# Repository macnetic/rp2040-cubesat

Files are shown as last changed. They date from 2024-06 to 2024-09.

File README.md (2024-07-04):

# rp2040-cubesat

> [!NOTE]  
> Preview this project on your browser with [KiCanvas](https://kicanvas.org/?github=https%3A%2F%2Fgithub.com%2Fmacnetic%2Frp2040-cubesat)!

## Requirements

| ID  | DESCRIPTION |
|-----|---|
| 001 | Device shall include a minimum of one RP2040 integrated circuit. |
| 002 | Dimensions shall conform with PCI/104 form factor. |
| 003 | Device shall supply 1 external UART interface. |
| 004 | Device shall supply 1 external CAN interface. |
| 005 | Device shall supply 1 on-board SPI interface. |
| 006 | Device shall supply 1 on-board I2C interface. |
| 007 | Device shall use a TCXO to generate a stable reference clock. |

## External interfaces

- UART (PHY TBD)
- CAN
- ARM CoreSight-10

## Schematic strategy

The schematics for this project is laid out across multiple sheets. 
The top-level sheets contain functional block diagrams. 
The functional circuit blocks themselves are implemented in the lower-level sheets.

## PCB Layout strategy

A 4-layer controlled impedance stackup is used.

|Layer | Designation |
|---|---|
| L1 (Top) | SIG |
| L2 | GND |
| L3 | GND |
| L3 (Bottom)| SIG+PWR |

Functional circuit blocks are routed first. The blocks are then laid out and connected.

High-speed electrical interfaces are routed with controlled impedance transmission lines.

Priority is given to routing high-speed interfaces.

Sensitive analog circuitry is separated from digital circuitry.

## References

[1] [CubeSat Information - CubeSat.org](https://www.cubesat.org/cubesatinfo)

[2] [CubeSat Kit PCB Specification](https://web.archive.org/web/20220302180556/http://www.cubesatkit.com/docs/CSK_PCB_Spec-A5.pdf) (archived from the original at http://www.cubesatkit.com/docs/CSK_PCB_Spec-A5.pdf)

[3] [RP2040 Documentation](https://www.raspberrypi.com/documentation/microcontrollers/rp2040.html)

[4]

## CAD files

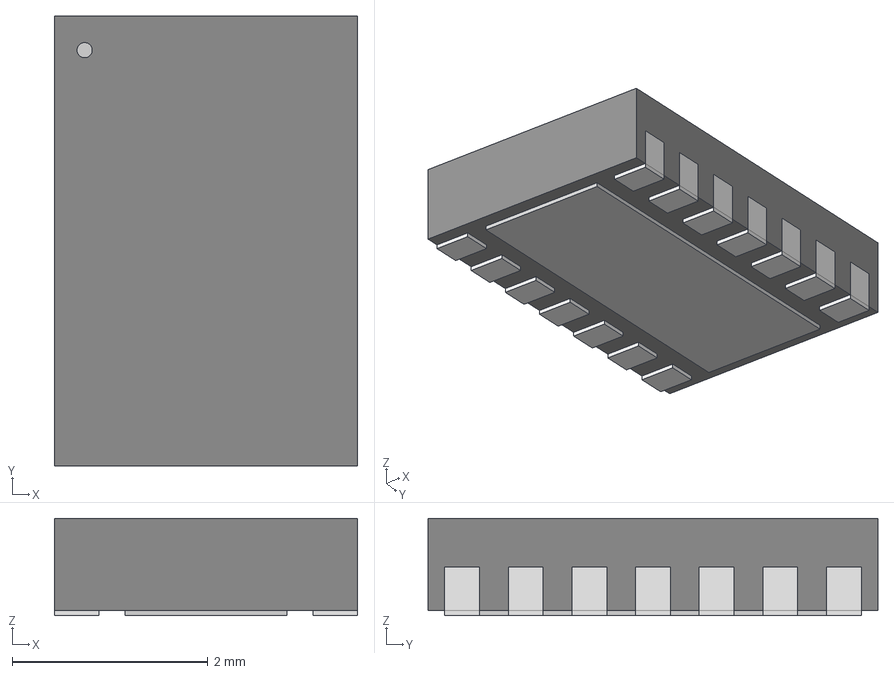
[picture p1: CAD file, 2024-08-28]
footprints/HVSON14_TJA1059_NXP.step
3.10 x 4.60 x 0.993 mm

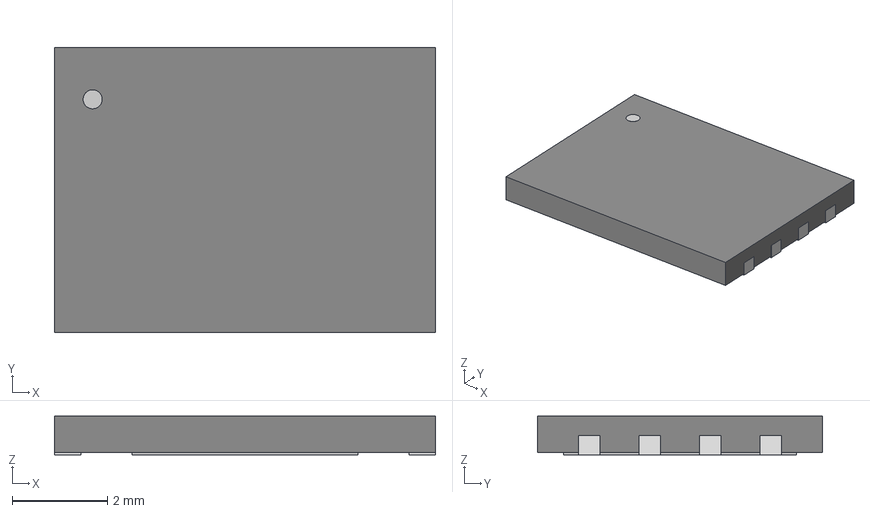
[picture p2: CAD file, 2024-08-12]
footprints/SON8_S25FL128SAGNFI001_INF.step
8.00 x 5.99 x 0.815 mm

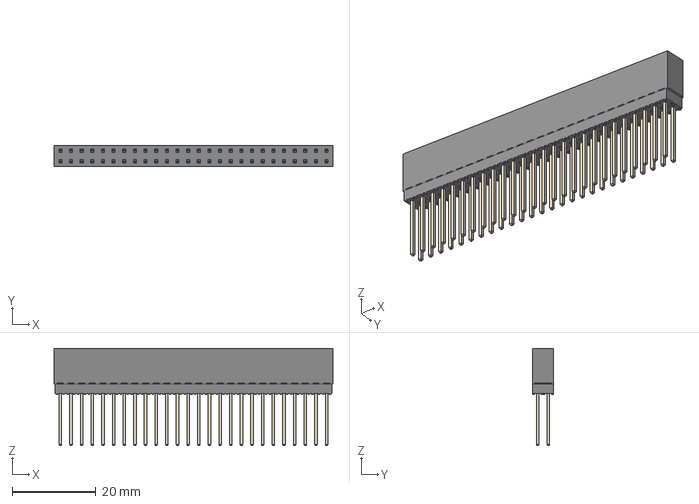
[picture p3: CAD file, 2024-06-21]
footprints/ESQ-126-39-G-D.step
66.5 x 5.08 x 23.2 mm

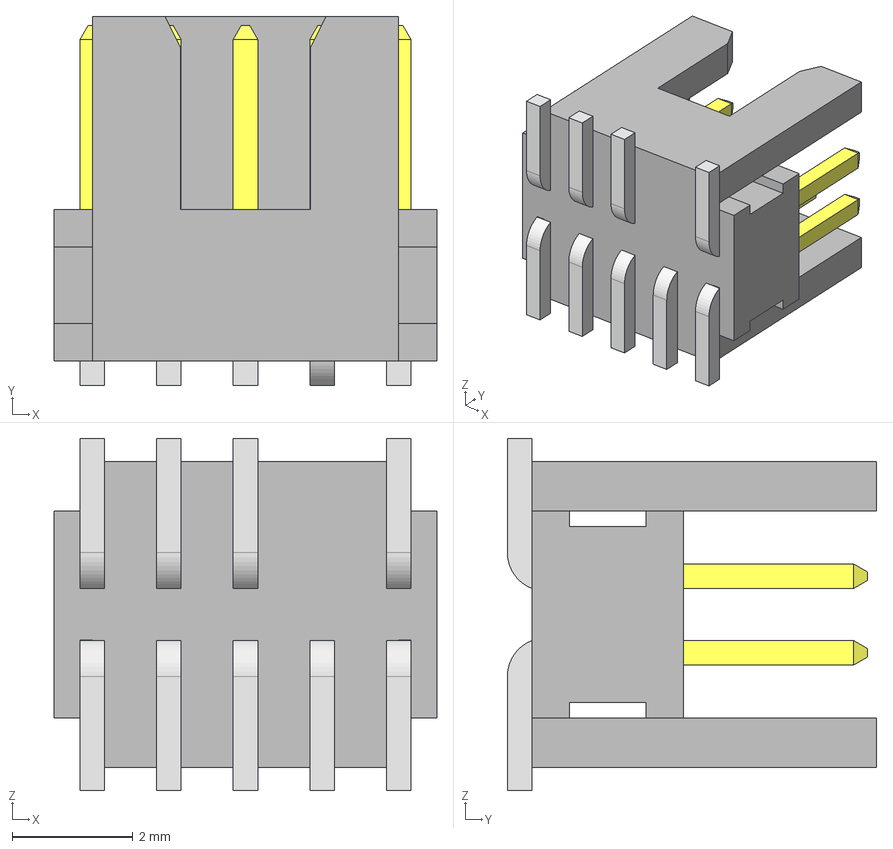
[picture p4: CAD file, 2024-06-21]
footprints/FTSH-105-01-L-DV-007.step
6.35 x 6.12 x 5.84 mm
FTSH-105-01-L-DV-007-K_pins2
FTSH-105-01-L-DV-007-K_pins1
FTSH-105-01-L-DV-007-K_body

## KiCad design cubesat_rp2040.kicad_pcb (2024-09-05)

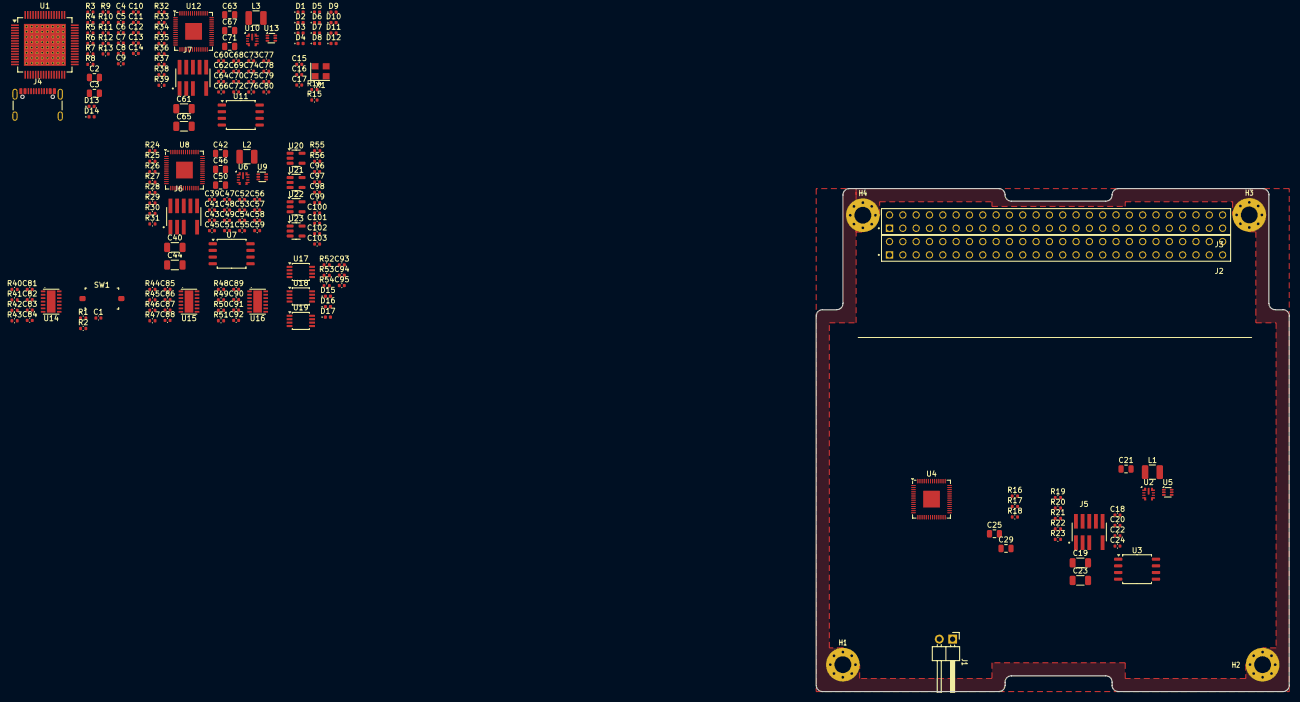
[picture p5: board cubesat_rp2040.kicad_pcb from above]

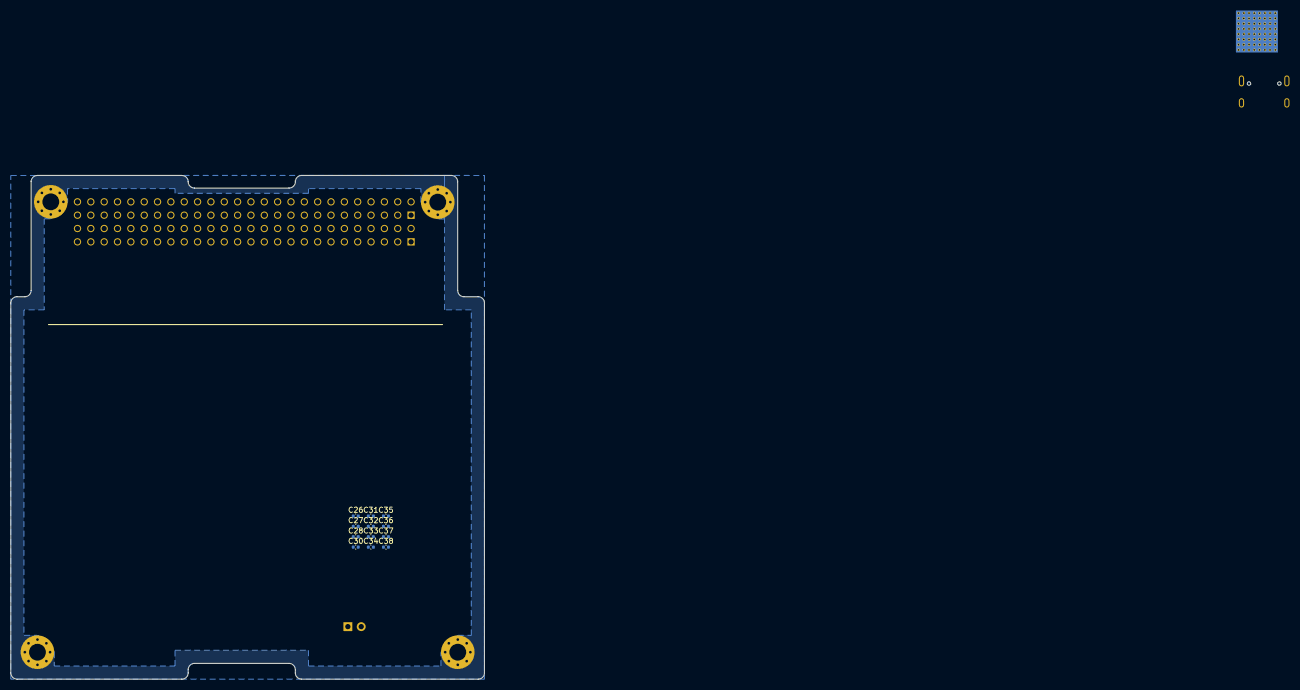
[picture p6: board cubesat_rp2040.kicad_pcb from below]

Board: 6 copper layers, 90.2 x 95.9 mm, 215 parts (12 on the bottom side), 138 nets, no tracks yet.

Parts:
C1, C4, C5, C6, C7, C8, C9, C10, C11, C12, C13, C14, C15, C16, C18, C20, C22, C24, C26, C27, C28, C30, C31, C32, C33, C34, C35, C36, C37, C38, C39, C41, C43, C45, C47, C48, C49, C51, C52, C53, C54, C55, C56, C57, C58, C59, C60, C62, C64, C66, C68, C69, C70, C72, C73, C74, C75, C76, C77, C78, C79, C80, C81, C82, C85, C86, C89, C90, C93, C94, C95, C96, C97, C98, C99: 100nF; C_0402_1005Metric
C2, C3, C21, C25, C29, C42, C46, C50, C63, C67, C71: 1uF; C_0805_2012Metric
C17: 15pF; C_0402_1005Metric
C19, C23, C40, C44, C61, C65: 10uF; C_1206_3216Metric
C83, C84, C87, C88, C91, C92: 4.7nF; C_0402_1005Metric
C100, C101, C102, C103: 1nF; C_0402_1005Metric
D1, D2, D3, D4, D5, D6, D7, D8, D9, D10, D11, D12, D13, D14: D_TVS; D_0402_1005Metric
D15, D16, D17: RED; LED_0402_1005Metric
H1, H2, H3, H4: MountingHole_Pad; MountingHole_3.2mm_M3_Pad_Via
J1: Conn_01x02; PinHeader_1x02_P2.54mm_Horizontal
J2, J3: ESQ-126-39-G-D; SAMTEC_ESQ-126-39-G-D_CUBESAT
J4: USB_C_Receptacle_USB2.0; USB_C_Receptacle_GCT_USB4105-xx-A_16P_TopMnt_Horizontal
J5, J6, J7: FTSH-105-01-L-DV-007-K; SAMTEC_FTSH-105-01-L-DV-007
L1, L2, L3: 15uH; L_1210_3225Metric
R1, R19, R20, R21, R22, R23, R27, R28, R29, R30, R31, R35, R36, R37, R38, R39: 100kR; R_0402_1005Metric
R2: 10kR; R_0402_1005Metric
R3, R4: 5.1kR 10%; R_0402_1005Metric
R5: 90.9kR 1%; R_0402_1005Metric
R6, R9, R10, R11, R12, R13: 4.7kR; R_0402_1005Metric
R7: 10kR 1%; R_0402_1005Metric
R8: 9.53kR 1%; R_0402_1005Metric
R14: 33R; R_0402_1005Metric
R15: 88.7R; R_0402_1005Metric
R16, R24, R32: 1kR; R_0402_1005Metric
R17, R18, R25, R26, R33, R34: 27R; R_0402_1005Metric
R40, R41, R42, R43, R44, R45, R46, R47, R48, R49, R50, R51: 60R; R_0402_1005Metric
R52, R53, R54: 470R; R_0402_1005Metric
R55, R56: 100R; R_0402_1005Metric
SW1: SW_Push; SW_Push_SPST_XKB_TS-1101-X-X
U1: TUSB4041I; HTQFP-64-1EP_10x10mm_P0.5mm_EP8x8mm_Mask4.4x4.4mm_ThermalVi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
U2, U6, U10: LMR36503MSC3RPERQ1; TI_VQFN-HR_2.1x2.1mm_P0.5mm
U3, U7, U11: IS25LP128F; SOIC-8_5.275x5.275mm_P1.27mm
U4, U8, U12: RP2040; QFN-56-1EP_7x7mm_P0.4mm_EP3.2x3.2mm
U5, U9, U13: 74LVC1G11; SOT-563
U14, U15, U16: TCAN1048AV-Q1; SOT1086-2_HVSON14_4.5x3x0.85mm_P0.65mm
U17, U18, U19: 74LVC2G38; TSSOP-8_3x3mm_P0.65mm
U20, U21: SN65LVDS1DBV; SOT-23-5
U22, U23: SN65LVDS2DBV; SOT-23-5
X1: YSO140TC; Oscillator_SMD_YXC_YSO140TC_4Pin_3.2x2.5mm

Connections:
+1V1: C2.1, C4.1, C5.1, C6.1, C7.1, C8.1, C9.1, C10.1, U1.19 (VDD), U1.25 (VDD), U1.37 (VDD), U1.45 (VDD), U1.53 (VDD), U1.60 (VDD), U1.63 (VDD)
+3V3: C3.1, C11.1, C12.1, C13.1, C14.1, C82.1, C86.1, C90.1, C93.1, C94.1, C95.1, R1.1, R14.1, R52.1, R53.1, R54.1, U1.2 (VDD33), U1.20 (VDD33), U1.31 (VDD33), U1.48 (VDD33), U14.11 (VIO), U15.11 (VIO), U16.11 (VIO), U17.8 (VCC), U18.8 (VCC), U19.8 (VCC)
+5V: C81.1, C85.1, C89.1, U14.3 (VCC), U15.3 (VCC), U16.3 (VCC)
/BOOTSEL: J1.1, R16.2, R24.2, R32.2
/CAN PHY - UNIT A/CAN_A.N: D2.2 (A2), J2.01, R41.1, R45.1, R49.1, U14.12 (CANL1), U15.12 (CANL1), U16.12 (CANL1)
/CAN PHY - UNIT A/CAN_A.P: D1.2 (A2), J2.03, R40.1, R44.1, R48.1, U14.13 (CANH1), U15.13 (CANH1), U16.13 (CANH1)
/CAN PHY - UNIT A/CAN_A.RXD: U4.16 (GPIO13), U14.4 (RXD1)
/CAN PHY - UNIT A/CAN_A.TXD: U4.17 (GPIO14), U14.1 (TXD1)
/CAN PHY - UNIT A/CAN_A.~STB: U4.18 (GPIO15), U14.14 (~STB1)
/CAN PHY - UNIT A/CAN_B.N: D4.2 (A2), J2.02, R43.1, R47.1, R51.1, U14.9 (CANL2), U15.9 (CANL2), U16.9 (CANL2)
/CAN PHY - UNIT A/CAN_B.P: D3.2 (A2), J2.04, R42.1, R46.1, R50.1, U14.10 (CANH2), U15.10 (CANH2), U16.10 (CANH2)
/CAN PHY - UNIT A/CAN_B.RXD: U4.14 (GPIO11), U14.7 (RXD2)
/CAN PHY - UNIT A/CAN_B.TXD: U4.15 (GPIO12), U14.6 (TXD2)
/CAN PHY - UNIT A/CAN_B.~STB: U4.13 (GPIO10), U14.8 (~STB2)
/CAN PHY - UNIT B/CAN_A.RXD: U8.16 (GPIO13), U15.4 (RXD1)
/CAN PHY - UNIT B/CAN_A.TXD: U8.17 (GPIO14), U15.1 (TXD1)
/CAN PHY - UNIT B/CAN_A.~STB: U8.18 (GPIO15), U15.14 (~STB1)
/CAN PHY - UNIT B/CAN_B.RXD: U8.14 (GPIO11), U15.7 (RXD2)
/CAN PHY - UNIT B/CAN_B.TXD: U8.15 (GPIO12), U15.6 (TXD2)
/CAN PHY - UNIT B/CAN_B.~STB: U8.13 (GPIO10), U15.8 (~STB2)
/CAN PHY - UNIT C/CAN_A.RXD: U12.16 (GPIO13), U16.4 (RXD1)
/CAN PHY - UNIT C/CAN_A.TXD: U12.17 (GPIO14), U16.1 (TXD1)
/CAN PHY - UNIT C/CAN_A.~STB: U12.18 (GPIO15), U16.14 (~STB1)
/CAN PHY - UNIT C/CAN_B.RXD: U12.14 (GPIO11), U16.7 (RXD2)
/CAN PHY - UNIT C/CAN_B.TXD: U12.15 (GPIO12), U16.6 (TXD2)
/CAN PHY - UNIT C/CAN_B.~STB: U12.13 (GPIO10), U16.8 (~STB2)
/Cubesat System Bus/+3V3: J2.27, J2.28
/Cubesat System Bus/+5V: J2.25, J2.26, J3.25, J3.26
/Cubesat System Bus/CHARGE: J2.31, J2.32
/Cubesat System Bus/UART_A.D+: D5.2 (A2), J2.05
/Cubesat System Bus/UART_A.D-: D6.2 (A2), J2.07
/Cubesat System Bus/UART_B.D+: D7.2 (A2), J2.06
/Cubesat System Bus/UART_B.D-: D8.2 (A2), J2.08
/Cubesat System Bus/UART_C.D+: D9.2 (A2), J2.13
/Cubesat System Bus/UART_C.D-: D10.2 (A2), J2.15
/Cubesat System Bus/UART_D.D+: D11.2 (A2), J2.22
/Cubesat System Bus/UART_D.D-: D12.2 (A2), J2.24
/Cubesat System Bus/VBAT: J3.45, J3.46
/LVDS/+3V3_UNIT: C96.1, C97.1, C98.1, C99.1, C100.1, C101.1, C102.1, C103.1, U20.1 (V_{CC}), U21.1 (V_{CC}), U22.1 (V_{CC}), U23.1 (V_{CC})
/LVDS/LVDS_RX_A.N: R55.2, U22.4 (B)
/LVDS/LVDS_RX_A.P: R55.1, U22.3 (A)
/LVDS/LVDS_RX_B.N: R56.2, U23.4 (B)
/LVDS/LVDS_RX_B.P: R56.1, U23.3 (A)
/Oscillator/24M0_CLK: C17.2, R15.2, U1.30 (XI), U4.20 (XIN), U8.20 (XIN), U12.20 (XIN)
/RP2040 - Unit A/+1V1_UNIT: C25.1, C26.1, C27.1, C28.1, U4.23 (DVDD), U4.45 (VREG_VOUT), U4.50 (DVDD)
/RP2040 - Unit A/+3V3_UNIT: C18.1, C23.1, C24.1, C29.1, C30.1, C31.1, C32.1, C33.1, C34.1, C35.1, C36.1, C37.1, C38.1, J5.01 (VTREF), L1.2, R19.2, R21.1, R22.1, R23.1, U2.8 (FB), U3.8 (VCC), U4.1 (IOVDD), U4.10 (IOVDD), U4.22 (IOVDD), U4.33 (IOVDD), U4.42 (IOVDD), U4.43 (ADC_AVDD), U4.44 (VREG_VIN), U4.48 (USB_VDD), U4.49 (IOVDD), U5.5 (VCC)
/RP2040 - Unit A/BOOT: C22.1, U2.6 (BOOT)
/RP2040 - Unit A/QSPI.SCLK: U3.6 (SCK), U4.52 (QSPI_SCLK)
/RP2040 - Unit A/QSPI.SD0: U3.5 (SI/IO0), U4.53 (QSPI_SD0)
/RP2040 - Unit A/QSPI.SD1: U3.2 (SO/IO1), U4.55 (QSPI_SD1)
/RP2040 - Unit A/QSPI.SD2: U3.3 (~WP/IO2), U4.54 (QSPI_SD2)
/RP2040 - Unit A/QSPI.SD3: U3.7 (~HOLD/IO3), U4.51 (QSPI_SD3)
/RP2040 - Unit A/QSPI.~SS: R16.1, U3.1 (~CE), U4.56 (QSPI_SS)
/RP2040 - Unit A/RP_USB.D+: R17.2, U4.47 (USB_DP)
/RP2040 - Unit A/RP_USB.D-: R18.2, U4.46 (USB_DM)
/RP2040 - Unit A/SW: C22.2, L1.1, U2.5 (SW)
/RP2040 - Unit A/SWCLK: J5.04 (TCK/SWCLK), R20.2, U4.24 (SWCLK)
/RP2040 - Unit A/SWDIO: J5.02 (TMS/SWDIO), R19.1, U4.25 (SWD)
/RP2040 - Unit A/TMR_VOTE_1: U4.38 (GPIO26_ADC0), U17.5, U18.1
/RP2040 - Unit A/TMR_VOTE_2: U4.39 (GPIO27_ADC1), U18.5, U19.1
/RP2040 - Unit A/USB.D+: R17.1, U1.56 (USB_DP_DN4)
/RP2040 - Unit A/USB.D-: R18.1, U1.57 (USB_DM_DN4)
/RP2040 - Unit A/~PWR_RESET: R22.2, U2.2 (PGOOD), U5.1
/RP2040 - Unit A/~RESET: U4.26 (RUN), U5.4
/RP2040 - Unit B/+1V1_UNIT: C46.1, C47.1, C48.1, C49.1, U8.23 (DVDD), U8.45 (VREG_VOUT), U8.50 (DVDD)
/RP2040 - Unit B/+3V3_UNIT: C39.1, C44.1, C45.1, C50.1, C51.1, C52.1, C53.1, C54.1, C55.1, C56.1, C57.1, C58.1, C59.1, J6.01 (VTREF), L2.2, R27.2, R29.1, R30.1, R31.1, U6.8 (FB), U7.8 (VCC), U8.1 (IOVDD), U8.10 (IOVDD), U8.22 (IOVDD), U8.33 (IOVDD), U8.42 (IOVDD), U8.43 (ADC_AVDD), U8.44 (VREG_VIN), U8.48 (USB_VDD), U8.49 (IOVDD), U9.5 (VCC)
/RP2040 - Unit B/BOOT: C43.1, U6.6 (BOOT)
/RP2040 - Unit B/QSPI.SCLK: U7.6 (SCK), U8.52 (QSPI_SCLK)
/RP2040 - Unit B/QSPI.SD0: U7.5 (SI/IO0), U8.53 (QSPI_SD0)
/RP2040 - Unit B/QSPI.SD1: U7.2 (SO/IO1), U8.55 (QSPI_SD1)
/RP2040 - Unit B/QSPI.SD2: U7.3 (~WP/IO2), U8.54 (QSPI_SD2)
/RP2040 - Unit B/QSPI.SD3: U7.7 (~HOLD/IO3), U8.51 (QSPI_SD3)
/RP2040 - Unit B/QSPI.~SS: R24.1, U7.1 (~CE), U8.56 (QSPI_SS)
/RP2040 - Unit B/RP_USB.D+: R25.2, U8.47 (USB_DP)
/RP2040 - Unit B/RP_USB.D-: R26.2, U8.46 (USB_DM)
/RP2040 - Unit B/SW: C43.2, L2.1, U6.5 (SW)
/RP2040 - Unit B/SWCLK: J6.04 (TCK/SWCLK), R28.2, U8.24 (SWCLK)
/RP2040 - Unit B/SWDIO: J6.02 (TMS/SWDIO), R27.1, U8.25 (SWD)
/RP2040 - Unit B/TMR_VOTE_1: U8.38 (GPIO26_ADC0), U17.1, U19.5
/RP2040 - Unit B/TMR_VOTE_2: U8.39 (GPIO27_ADC1), U18.6, U19.2
/RP2040 - Unit B/USB.D+: R25.1, U1.49 (USB_DP_DN3)
/RP2040 - Unit B/USB.D-: R26.1, U1.50 (USB_DM_DN3)
/RP2040 - Unit B/~PWR_RESET: R30.2, U6.2 (PGOOD), U9.1
/RP2040 - Unit B/~RESET: U8.26 (RUN), U9.4
/RP2040 - Unit C/+1V1_UNIT: C67.1, C68.1, C69.1, C70.1, U12.23 (DVDD), U12.45 (VREG_VOUT), U12.50 (DVDD)
/RP2040 - Unit C/+3V3_UNIT: C60.1, C65.1, C66.1, C71.1, C72.1, C73.1, C74.1, C75.1, C76.1, C77.1, C78.1, C79.1, C80.1, J7.01 (VTREF), L3.2, R35.2, R37.1, R38.1, R39.1, U10.8 (FB), U11.8 (VCC), U12.1 (IOVDD), U12.10 (IOVDD), U12.22 (IOVDD), U12.33 (IOVDD), U12.42 (IOVDD), U12.43 (ADC_AVDD), U12.44 (VREG_VIN), U12.48 (USB_VDD), U12.49 (IOVDD), U13.5 (VCC)
/RP2040 - Unit C/BOOT: C64.1, U10.6 (BOOT)
/RP2040 - Unit C/QSPI.SCLK: U11.6 (SCK), U12.52 (QSPI_SCLK)
/RP2040 - Unit C/QSPI.SD0: U11.5 (SI/IO0), U12.53 (QSPI_SD0)
/RP2040 - Unit C/QSPI.SD1: U11.2 (SO/IO1), U12.55 (QSPI_SD1)
/RP2040 - Unit C/QSPI.SD2: U11.3 (~WP/IO2), U12.54 (QSPI_SD2)
/RP2040 - Unit C/QSPI.SD3: U11.7 (~HOLD/IO3), U12.51 (QSPI_SD3)
/RP2040 - Unit C/QSPI.~SS: R32.1, U11.1 (~CE), U12.56 (QSPI_SS)
/RP2040 - Unit C/RP_USB.D+: R33.2, U12.47 (USB_DP)
/RP2040 - Unit C/RP_USB.D-: R34.2, U12.46 (USB_DM)
/RP2040 - Unit C/SW: C64.2, L3.1, U10.5 (SW)
/RP2040 - Unit C/SWCLK: J7.04 (TCK/SWCLK), R36.2, U12.24 (SWCLK)
/RP2040 - Unit C/SWDIO: J7.02 (TMS/SWDIO), R35.1, U12.25 (SWD)
/RP2040 - Unit C/TMR_VOTE_1: U12.38 (GPIO26_ADC0), U17.2, U19.6
/RP2040 - Unit C/TMR_VOTE_2: U12.39 (GPIO27_ADC1), U17.6, U18.2
/RP2040 - Unit C/USB.D+: R33.1, U1.41 (USB_DP_DN2)
/RP2040 - Unit C/USB.D-: R34.1, U1.42 (USB_DM_DN2)
/RP2040 - Unit C/~PWR_RESET: R38.2, U10.2 (PGOOD), U13.1
/RP2040 - Unit C/~RESET: U12.26 (RUN), U13.4
/TMR/~TMR_RESET_A: D15.1 (K), R23.2, U5.6, U17.7, U19.3
/TMR/~TMR_RESET_B: D16.1 (K), R31.2, U9.6, U17.3, U18.7
/TMR/~TMR_RESET_C: D17.1 (K), R39.2, U13.6, U18.3, U19.7
/USB/PWRCTL1/BATEN1: R13.1, U1.4 (PWRCTL1/BATEN1)
/USB/PWRCTL2/BATEN2: R12.1, U1.3 (PWRCTL2/BATEN2)
/USB/PWRCTL3/BATEN3: R11.1, U1.1 (PWRCTL3/BATEN3)
/USB/PWRCTL4/BATEN4: R10.1, U1.64 (PWRCTL4/BATEN4)
/USB/USB_UP.CC1: J4.A5 (CC1), R4.1
/USB/USB_UP.CC2: J4.B5 (CC2), R3.1
/USB/USB_UP.D+: D13.2 (A2), J4.A6 (D+), J4.B6 (D+), U1.21 (USB_DP_UP)
/USB/USB_UP.D-: D14.2 (A2), J4.A7 (D-), J4.B7 (D-), U1.22 (USB_DM_UP)
/USB/USB_VBUS: R5.2, R7.1, U1.16 (USB_VBUS)
/~USR_RESET: C1.1, J5.10 (nSRST), J6.10 (nSRST), J7.10 (nSRST), R2.1, R21.2, R29.2, R37.2, U1.18 (GRSTz), U5.3, U9.3, U13.3
GND: C1.2, C2.2, C3.2, C4.2, C5.2, C6.2, C7.2, C8.2, C9.2, C10.2, C11.2, C12.2, C13.2, C14.2, C15.2, C17.1, C18.2, C19.2, C20.2, C21.2, C23.2, C24.2, C25.2, C26.2, C27.2, C28.2, C29.2, C30.2, C31.2, C32.2, C33.2, C34.2, C35.2, C36.2, C37.2, C38.2, C39.2, C40.2, C41.2, C42.2, C44.2, C45.2, C46.2, C47.2, C48.2, C49.2, C50.2, C51.2, C52.2, C53.2, C54.2, C55.2, C56.2, C57.2, C58.2, C59.2, C60.2, C61.2, C62.2, C63.2, C65.2, C66.2, C67.2, C68.2, C69.2, C70.2, C71.2, C72.2, C73.2, C74.2, C75.2, C76.2, C77.2, C78.2, C79.2, C80.2, C81.2, C82.2, C83.1, C84.1, C85.2, C86.2, C87.1, C88.1, C89.2, C90.2, C91.1, C92.1, C93.2, C94.2, C95.2, C96.2, C97.2, C98.2, C99.2, C100.2, C101.2, C102.2, C103.2, D1.1 (A1), D2.1 (A1), D3.1 (A1), D4.1 (A1), D5.1 (A1), D6.1 (A1), D7.1 (A1), D8.1 (A1), D9.1 (A1), D10.1 (A1), D11.1 (A1), D12.1 (A1), D13.1 (A1), D14.1 (A1), H1.1, H2.1, H3.1, H4.1, J1.2, J2.33, J2.34, J3.29, J3.30, J3.31, J3.32, J4.A1 (GND), J4.A12 (GND), J4.B1 (GND), J4.B12 (GND), J4.S1 (SHIELD), J5.03 (GND), J5.05 (GND), J5.09 (GND), J6.03 (GND), J6.05 (GND), J6.09 (GND), J7.03 (GND), J7.05 (GND), J7.09 (GND), R3.2, R4.2, R6.2, R7.2, R8.2, R9.2, R10.2, R11.2, R12.2, R13.2, R20.1, R28.1, R36.1, SW1.1, U1.65 (VSS), U2.9 (GND), U3.4 (GND), U4.57 (GND), U5.2 (GND), U6.9 (GND), U7.4 (GND), U8.57 (GND), U9.2 (GND), U10.9 (GND), U11.4 (GND), U12.57 (GND), U13.2 (GND), U14.2 (GND), U14.5 (GND), U14.15 (EP), U15.2 (GND), U15.5 (GND), U15.15 (EP), U16.2 (GND), U16.5 (GND), U16.15 (EP), U17.4 (GND), U18.4 (GND), U19.4 (GND), U20.2 (GND), U21.2 (GND), U22.2 (GND), U23.2 (GND), X1.2 (GND)
unnamed: C16.2, R15.1
unnamed: C83.2, R40.2, R41.2
unnamed: C84.2, R42.2, R43.2
unnamed: C87.2, R44.2, R45.2
unnamed: C88.2, R46.2, R47.2
unnamed: C91.2, R48.2, R49.2
unnamed: C92.2, R50.2, R51.2
unnamed: D15.2 (A), R52.2
unnamed: D16.2 (A), R53.2
unnamed: D17.2 (A), R54.2
unnamed: R1.2, R2.2, SW1.2
unnamed: R9.1, U1.13 (AUTOENz/HS_SUSPEND)
unnamed: R6.1, U1.10 (GANGED/SMBA2/HS_UP)
unnamed: R8.1, U1.32 (USB_R1)
unnamed: C21.1, U2.1 (MODE/SYNC), U2.7 (VCC)
unnamed: C42.1, U6.1 (MODE/SYNC), U6.7 (VCC)
unnamed: C63.1, U10.1 (MODE/SYNC), U10.7 (VCC)
unnamed: C16.1, X1.3 (OUT)
unnamed: C15.1, R14.2, X1.4 (Vdd)
VBUS: C19.1, C20.1, C40.1, C41.1, C61.1, C62.1, J4.A4 (VBUS), J4.A9 (VBUS), J4.B4 (VBUS), J4.B9 (VBUS), R5.1, U2.3 (EN/UVLO), U2.4 (VIN), U6.3 (EN/UVLO), U6.4 (VIN), U10.3 (EN/UVLO), U10.4 (VIN)

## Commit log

2024-05-14 Upload existing files
    [ESQ-126-39-G-D.step, ESQ-126-39-G-D.stp, FTSH-105-01-L-DV-007-K.stp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]
2024-06-16 Update Kicad version and remove ignored files
    [ESQ-126-39-G-D.step, ESQ-126-39-G-D.stp, FTSH-105-01-L-DV-007-K.stp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]
2024-06-21 Revert breaking expected KiCAD project structure
    [ESQ-126-39-G-D.step, FTSH-105-01-L-DV-007-K.step, FTSH-105-01-L-DV-007.step]
2024-06-23 break out subcircuits, add switching regulator
    [cubesat_rp2040.kicad_pcb, cubesat_rp2040.kicad_sch, debug.kicad_sch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]
2024-06-24 Block diagram
    [cubesat_bus.kicad_sch, cubesat_rp2040.kicad_sch, debug.kicad_sch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]
2024-07-02 Complete power regulator schematics
    [cubesat_rp2040.kicad_pcb, cubesat_rp2040.kicad_sch, flash.kicad_sch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]
2024-07-03 Update footprints, route switching regulator circuit block
    [cubesat_rp2040.kicad_pcb, flash.kicad_sch, power.kicad_sch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]
2024-07-03 Update footprints, route more circuit blocks
    [cubesat_bus.kicad_sch, cubesat_rp2040.kicad_pcb, cubesat_rp2040.kicad_sch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]
2024-07-04 Update README, change footprints
    [cubesat_rp2040.kicad_pcb, reset.kicad_sch]
2024-07-16 Big update, bad commit messsage :)
    [L7983_5V_stepdown_3V3.kicad_sch, RST3225N_TCXO_32M0.kicad_sch, TUSB4041I_4-port_USB20_hub.kicad_sch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]
2024-08-12 Major update, everything has been touched
    [L7983_5V_stepdown_3V3.kicad_sch, RST3225N_TCXO_32M0.kicad_sch, SON8_S25FL128SAGNFI001_INF.step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]
2024-08-28 Another large revision, but we are getting closer
    [HVSON14_TJA1059_NXP.step, L7983_5V_stepdown_3V3.kicad_sch, RST3225N_TCXO_32M0.kicad_sch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]
2024-08-28 Clean up project
    [TUSB4041I_4-port_USB20_hub.kicad_sch, cubesat_bus.kicad_sch, cubesat_rp2040.kicad_sch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]
2024-09-05 More work on interfaces
    [can_phy_terminated.kicad_sch, can_phy_unterminated.kicad_sch, cubesat_rp2040.kicad_pcb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]

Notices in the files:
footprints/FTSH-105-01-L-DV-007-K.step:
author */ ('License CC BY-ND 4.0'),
